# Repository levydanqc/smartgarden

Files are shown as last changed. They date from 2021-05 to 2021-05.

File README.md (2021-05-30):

Quick links:

- [Latest release](https://github.com/levydanqc/smartgarden/releases/latest)
- [GitHub](https://github.com/levydanqc/smartgarden)
- [Arduino Projet](https://arduino-esp8266.readthedocs.io/en/latest/)
- [TODO](TODO.md)

===========================================

# SmartGardener

Smart garden monitoring system for growing vegetables and fruits with an NodeMcu and Blynk platform.

## My Story

At some points in life, we all tried to do some sort of gardening. Whether it is to embellish our house, to tried to grow some food or to prove to ourselves that we're able to take care of something else and not let it die, the process of planting some seeds in the ground isn't easy.
The problem is that humankind isn't the most reliable. How many of us forgot to take the cake out of the oven, to put the lid back on the peanut butter jar or even to water the plants and thought "Man ! Not again.". What if I told you there is an other way ? Today's technology let us automate virtually anything, from turning on and off the lights, brewing coffee each morning or cooking delicious meal.
Combining automation, micro-controllers and plants isn't new, there's plenty of projects on the internet about people trying to create their own garden monitoring system. Mine isn't that much different than theirs except that for one, almost everything is combined together. I've searched for a project where there would be soil moisture sensors, lights sensors, solenoid water valve, etc. as well as being able to control everything remotely before deciding to build my own.
It does work like I wanted, but there is so much more sensors and logic that I could and would like to add to this project, like TDS sensor (for water quality), controlling multiples valve for multiples garden, but one thing at a time.

## Connections

Because there's actually a lot of sensors (and I'm not that good with layout..), below is all the connections for the project.
_In the Schemas folder, there is a schema for the connections of each sensors._

| Board | Vin | Gnd | A0 | D0 | D1 | D2 | D5 | D6 | D7 |
| --- | :-: | :-: | :---: | :---: | :---: | :---: | :----: | :----: | :----: |
| NodeMcu | 12V | Gnd | MUX:COM(Z) | Flow:Data | DHT11:Data | Mosfet:Gate | MUX:S0 | MUX:S1 | MUX:S2 |

| Components  | Vcc | Gnd | COM (Z) | S0  | S1  | S2  | CH0 | CH1 | CH2  | CH3  |
| --- | :-: | :-: | :-----: | :-: | :-: | :-: | :-: | :-: | :--: | :--: |
| Multiplexer | 12V | Gnd | A0 | D5  | D6  | D7  | SM1 | SM2 | LDR1 | LDR2 |

| Components | Gate | Source |  Drain |
| --- | :---: | :----: | :---: |
| Mosfet | D2 (PU-10) |  Gnd | Valve[-] |

| Components | Positive | Negative | Data | Infos |
| --- | :---: | :---: | :--: | :---: |
| Power supply | Vin | Gnd | | |
| |  Valve | Gnd | | |
| | SD:In[+] | Gnd | | |
| Valve | 12V | Gnd | | |
| Diode | Valve[+] | Valve[-] | | |
| DHT11 | 3V | Gnd |  D1  | PU-10 |
| Soil Moisture 1 | 3V | Gnd | CH0  | |
| Soil Moisture 2 | 3V | Gnd | CH1  | |
| Photocell 1 | 3V | Gnd | CH2  | PD-1  |
| Photocell 2 | 3V | Gnd | CH3  | PD-1  |
| Flow Sensor | 3V | Gnd |  D0  | |

<dl>
  <dt>SM</dt>
  <dd>Soil Moisture Sensor.</dd>
  <dt>LDR</dt>
  <dd>Light Dependant Resistor (Photocell).</dd>
  <dt>MUX</dt>
  <dd>Multiplexer.</dd>
  <dt>SD</dt>
  <dd>Step-Down Converter.</dd>
  <dt>PU-Value</dt>
  <dd>Pull-Up Resistors of _Value_ kΩ.</dd>
  <dt>PD-Value</dt>
  <dd>Pull-Down Resistors of _Value_ kΩ.</dd>
</dl>

_12V refers to the power supply._ | _3V to the output of the NodeMcu._
_Ground connections are not important as long as they are wired together._ <br>
**Please make sure to double check your wiring before connecting the power supply as a wrong connection could fry your components. Also make sure to check all pull-down or pull-up resistors on the schema.**

## Configuration

To configure the project, all you need to do is enter your own informations from line 17 to 20. You will need the name and password of your WIFI and a hostname for the board as well as a password that you can create (It is optional, but for security purposes we were more comfortable using one).
The hostname will appear in the PORT setting of the Arduino IDE when you want to upload code and the password will be asked after compiling, just before uploading.

## Over-the-Air (OTA) Upload

The NodeMcu will be placed inside a waterproof and weather-resistant box near the plants and a power outlet so it won't be
easily accessible. A library called ArduinoOTA (Over-the-Air) let us upload new code to the board without being physically
connected to it, we only need to be in the same network for that to work.
The first upload need, obviously, to be wired to the board, but after that we can select the NodeMcu in the PORT configuration of the Arduino IDE to be connected to it.

**It is important to upload the OTA code and librairies each time to be sure it will still be accessible.**

## Flow Sensor

The flow sensor is being used primarily for testing the opening command of the valve.
It precision or accuracy isn't really what matters most as any value means the valve was opened and the system is working well.
His working principle is based on the Hall Effect: there is a rotor inside that makes loop when water goes though it with a magnet on one of the propeller and it outputs a signal each time the magnet complete one loop.

In the datasheet of the sensor there is coefficient often written like: `F = 7.5Q`. This number represents the quantity of water that has passed for each loop and is used to calculate the flow rate.

The formula is quite simple:

```
Flow rate (L/min) = Nb of loop for 1 sec / flow coefficient.
```

In this program, we used `attachInterrupt()` function from the arduino library that can asynchronously do a task when a physical pin receive a signal. Because of the way Blynk works we cannot use the `delay()` function to wait 1 second so instead, we began the interrupts (so that it increment a variable each time the signal is received) and at the next iteration we stop the interrupts and start calculate the flow rate using the actual time passed from the moment started it.

The adapted formula is then:

```
Flow rate (L/min) = ((1000.0 / (now() - start)) * count) / flowQ.
```

_We need to convert the number of loop from the nuber of seconds it was measure to 1 second._
_Where now() is the current time in unix (since epoch), start is the time we start counting signals (also in unix), count is the number of loop the magnet did and flowQ is the flow sensor coefficient._

## Soil Moisture Sensor

To calibrate the soil moisture sensor:

1. Put sensor in the air, retrieve value and set it to MOISTURE_AIR
2. Put sensor in water, retrieve value and set it to MOISTURE_WATER

## Solenoide Water Valve

The water valve need a 12V power supply and about 600 mA, but each items is different
so check your datasheet to be sure. Also, there is no polarity so you can connect either pin
to ground and positive.

## Mosfet IRF540N

A simple NPN transistor cannot take the power the solenoid valve needs, that is why a mosfet transistor is used. We control the solenoid valve with the Gate pin of the mosfet that, when HIGH, let current flow between Source and Drain.

## Multiplexer CD74HC4051

The NodeMcu only has one analog input, but there's 5 analog sensors to connect. That's when the multiplexer enter!
A multiplexer gives the possibility to connect multiples analog input to only one output. It does so by controlling which
sensor is poweredm (one at a time), reading its value and sending it before continuing to the next one.
This one has 8 channel, this means we can connect up to 8 analog inputs through the 8 pins _Y_ or _CH_ and output the value
through the _COM_ or _Z_ pin. We can tell it what channel to read from by controlling the state of the 3 _S_ pins, by pulling them
up in a specific way, it powered the matching channel.
Below is a table for each combination (it is basically a binary table with 3 bits):

| S0  | S1  | S2  | Channel |
| --- | :-: | :-: | :-----: |
| 0 |  0  |  0  | 0 |
| 1 |  0  |  0  | 1 |
| 0 |  1  |  0  | 2 |
| 1 |  1  |  0  | 3 |
| 0 |  0  |  1  | 4 |
| 1 |  0  |  1  | 5 |
| 0 |  1  |  1  | 6 |
| 1 |  1  |  1  | 7 |

## [Installation of Blynk Local Server](https://github.com/blynkkk/blynk-server)

For my project we used the Blynk Local Server. The installation can be found [on their GitHub](https://github.com/blynkkk/blynk-server) and it is pretty straight-forward.
The advantages of using your own local server is that you have a full control on what's happening, on the data that is being retrieved (could be
useful if like GPS was enabled on the app) so that your data isn't stored inside blynk server. Also, it is actually faster to use a local server
because of the distance the signal has to travel and more importantly, you can have as much Blynk Energy you want (so that you can customize your app by
adding an infinite number of widgets).

---

## © Copyright

<dl>
  <dt>Adidax: DHT11 Library</dt>
  <dd><a href="https://github.com/adidax/dht11">Github</a></dd>
  <dt>Blynkkk: Blynk-library</dt>
  <dd><a href="https://github.com/blynkkk/blynk-library">Github</a></dd>
  <dt>How2Electronics: TDS Meter</dt>
  <dd><a href="https://how2electronics.com/iot-based-tds-meter-using-esp8266-for-water-quality-monitoring/">Github</a></dd>
  <dt>The HookUp: GPIO_Limitations_ESP8266_NodeMCU.jpg</dt>
  <dd><a href="https://github.com/thehookup/Wireless_MQTT_Doorbell/blob/master/GPIO_Limitations_ESP8266_NodeMCU.jpg">Github</a></dd>
</dl>

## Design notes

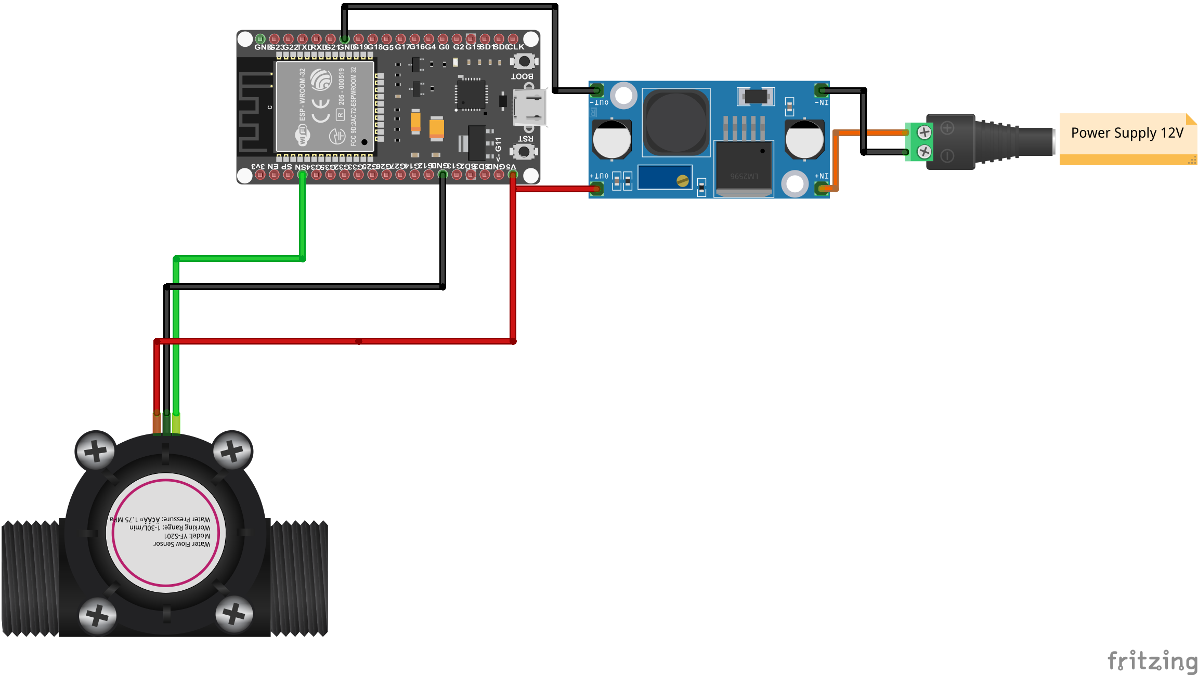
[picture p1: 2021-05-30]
Schematics/flow_sensor.png

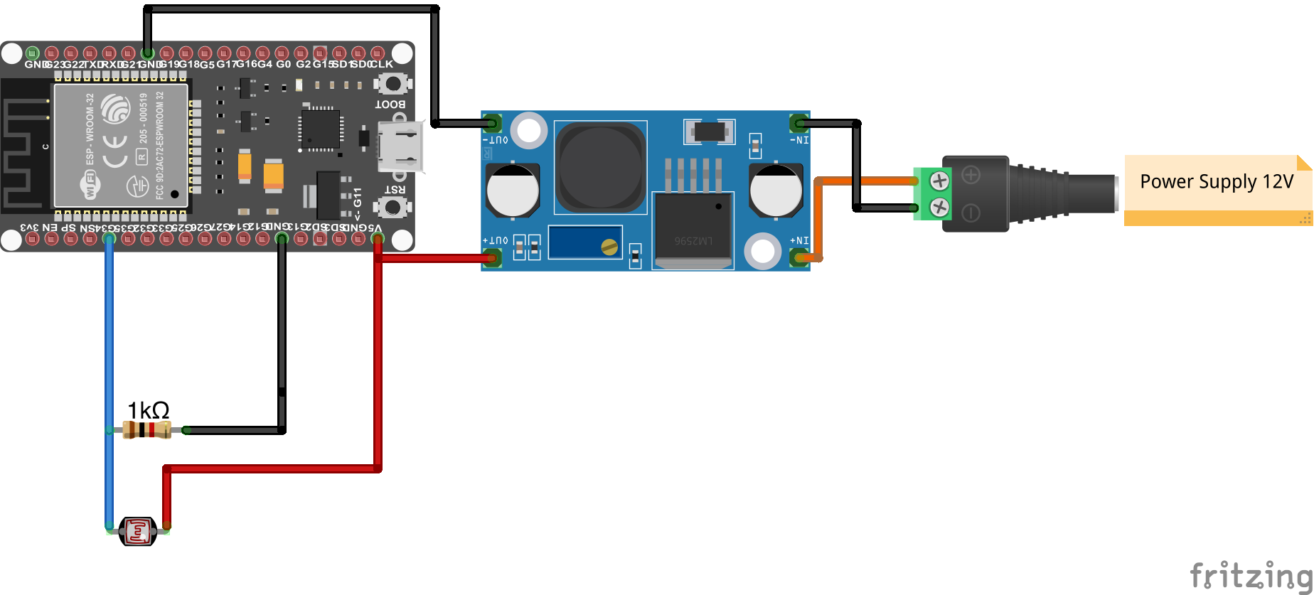
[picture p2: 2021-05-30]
Schematics/photocell.png

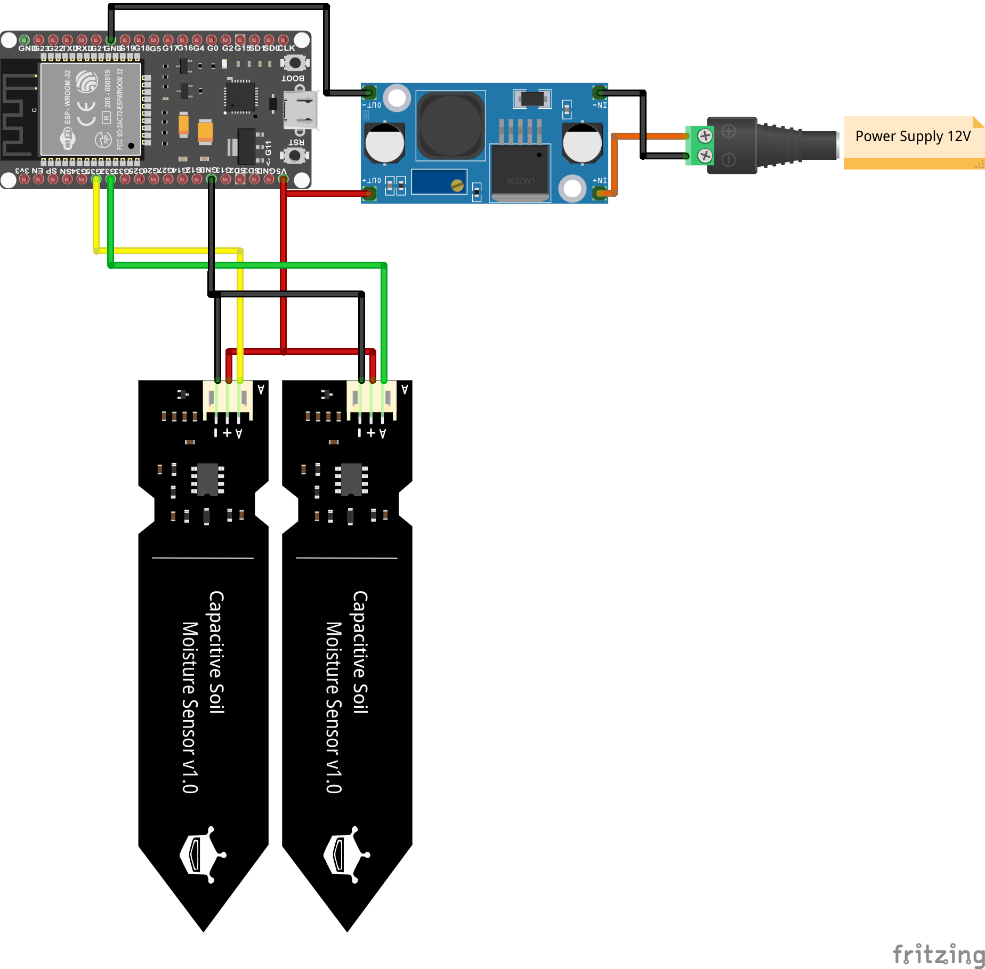
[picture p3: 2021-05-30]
Schematics/moisture_sensors.png

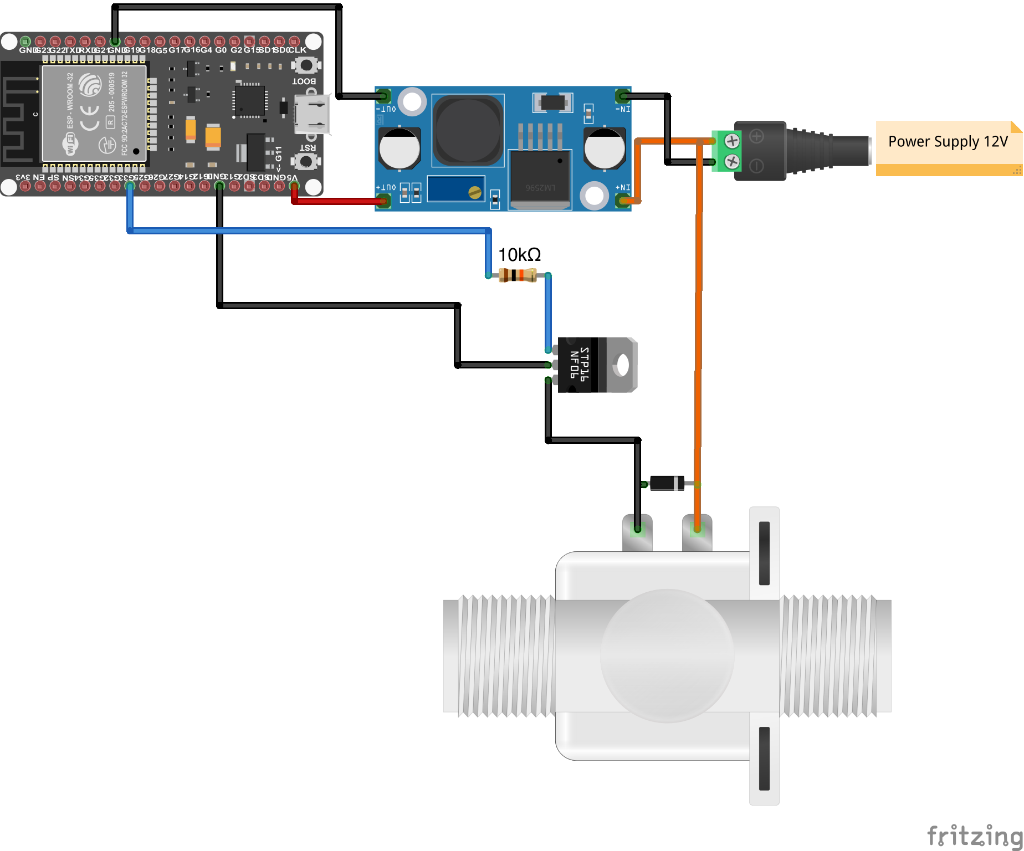
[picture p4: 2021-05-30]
Schematics/solenoid_valve.png

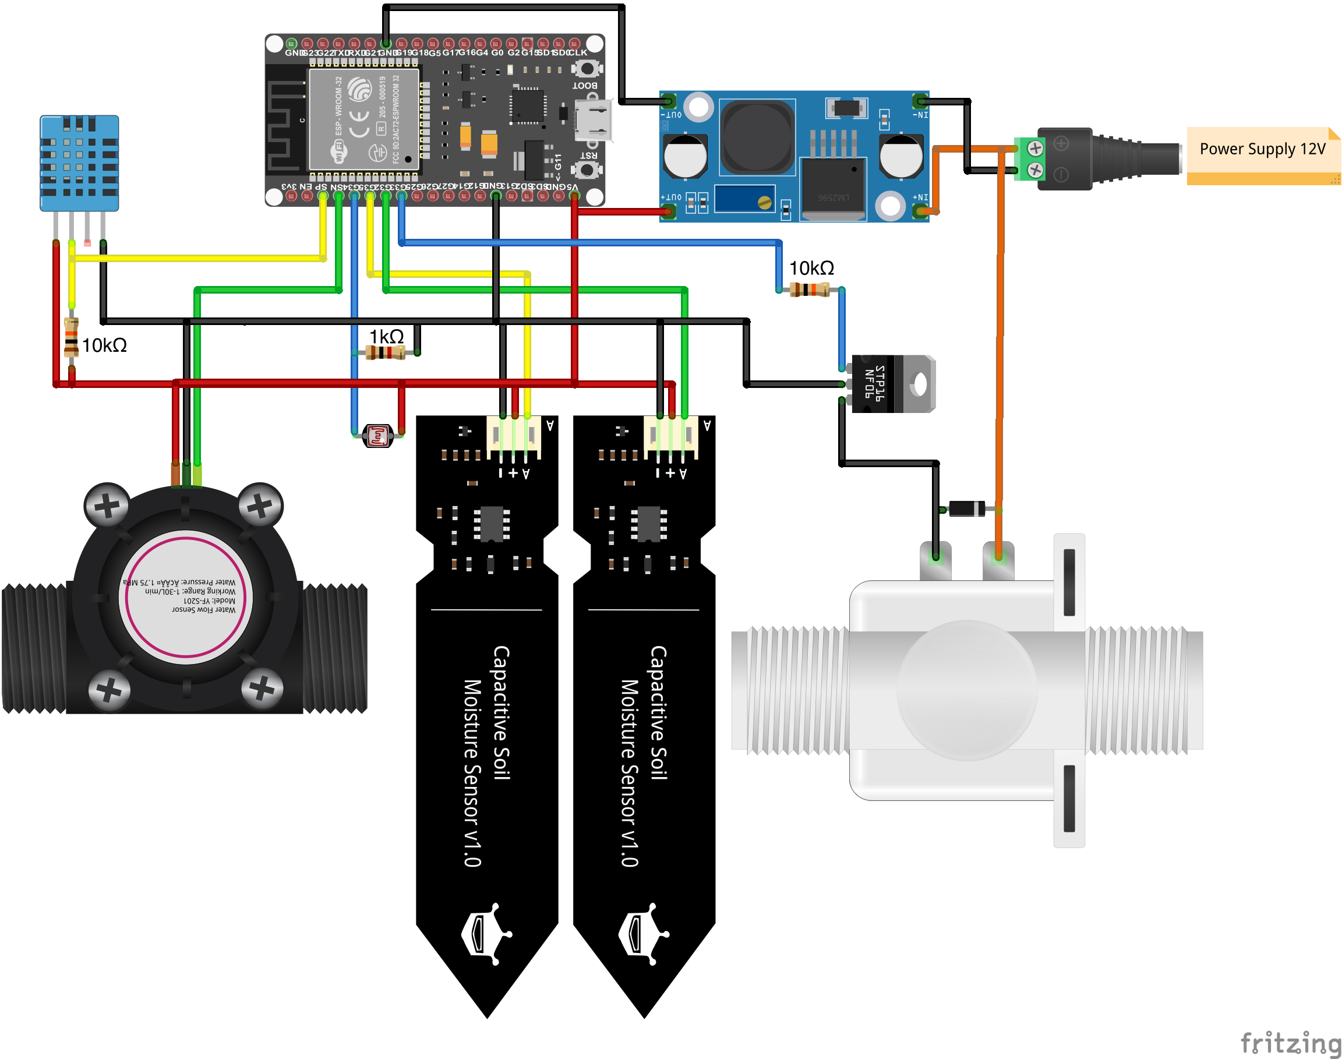
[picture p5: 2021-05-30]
Schematics/SmartGardener.png

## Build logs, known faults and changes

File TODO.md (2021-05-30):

# TODO list

Ideas of what to add for the future.

### In Progress

- [ ] Create file for soil moisture calibration

### For the future

- [ ] Get forecast weather
- [ ] Optimize variable size

### Done ✓

- [x] Switch valve with duration
- [x] Add a notification when online

### Personal Notes

Send notification with Blynk: Blynk.notify(message)
Send email with Blynk: Blynk.email("to@example.com", "Subject", "Your message goes here");

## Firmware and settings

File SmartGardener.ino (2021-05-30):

/***************************************************

 * Smart Garden Monitoring


 ** https://gitlab.com/levydanqc/smartgarden 

 ****************** Configuration ******************
Line 25:    SSID "PASSWORD_FOR_THE_ARDUINO"             -->     Name of your network
Line 26:    PASSW "YOUR_WIFI_PASSWORD":                 -->     Password of your network
Line 27:    ArduinoOTAHostname "NAME_FOR_THE_ARDUINO":  -->     Hostname for the OTA PORT setting
Line 28:    ArduinoOTAPASSW "PASSWORD_FOR_THE_ARDUINO": -->     Password for the OTA upload
Line 35:    char auth[] = "YOUR_BLYNK_TOKEN":           -->     Authentication token of the Blynk project

 ****************************************************
  © Copyright : see README.md
****************************************************/
/* 
 * Uncomment next line for debugging connection issues.
 * It will print to serial information about WIFI connection
 * and local server. 
*/
#define BLYNK_PRINT Serial

// ESP32
#include <WiFi.h>
#include <WiFiClient.h>
#include <BlynkSimpleEsp32.h>
#include <TimeLib.h>
#include <WidgetRTC.h>

// For OTA upload
#include <ESPmDNS.h>
#include <WiFiUdp.h>
#include <ArduinoOTA.h>

#include "dht11.h"

/* OTA Setup */
#ifndef SSID
#define SSID "YOUR_WIFI_SSID"                      // Enter the name of your network as it is in you WIFI settings
#define PASSW "YOUR_WIFI_PASSWORD"                 // Enter the password of your network
#define ArduinoOTAHostname "NAME_FOR_THE_ARDUINO"  // Enter the hostname for the board (Optional)
#define ArduinoOTAPASSW "PASSWORD_FOR_THE_ARDUINO" // Enter the password for the board (Optional)
#endif
const char *OtaSSID = SSID;
const char *OtaPassw = PASSW;
/* END OTA */

/* Blynk Setup*/
char auth[] = "YOUR_BLYNK_TOKEN";
char ssid[] = SSID;
char pass[] = PASSW;
BlynkTimer timer;
WidgetTerminal terminal(V13);
WidgetRTC rtc;
byte sliderValue;
float inputValue;
/* END Blynk */

/* Pinout */
#define valvePin 33
#define moisturePin1 32
#define moisturePin2 34
#define ldrPin 35
#define flowPin 39
#define dhtPin 36
/* END Pinout */

/* Function */
const byte inputs = 5;
float (*func[])(){
    getMoisture1,
    getMoisture2,
    getLDR,
    getFlow,
    getTemp,
    getHum};
/* END Function */

/* Valve */
unsigned long startValve;
int duration;
int valveIsActivated;
/* END Valve */

/* Flow Sensor */
volatile byte flowCounter;
float flowQ = 7.5;
float startFlow;
float flowRate;
/* END Flow */

/* DHT11 Sensor */
dht11 Dht;
float humidity;
float temperature;
/* END DHT11 */

/* Moisture Sensor */
#define MOISTURE_WATER 300
#define MOISTURE_AIR 670
float moisture1;
float moisture2;
/* END Moisture */

/* LDR */
#define LDR_MIN 0
#define LDR_MAX 1000
float ldr1;
/* END LDR */

void setup()
{
    Serial.begin(9600);

    /* OTA Setup */
    WiFi.mode(WIFI_STA);
    WiFi.begin(OtaSSID, OtaPassw);
    while (WiFi.waitForConnectResult() != WL_CONNECTED)
    {
        Serial.println("Connection Failed! Rebooting...");
        delay(5000);
        ESP.restart();
    }
    ArduinoOTA.setHostname(ArduinoOTAHostname);
    ArduinoOTA.setPassword(ArduinoOTAPASSW);
    /* END OTA */

    /* Blynk Setup */
    Blynk.begin(auth, ssid, pass, "192.168.1.100", 8080);
    timer.setInterval(1000L, sendData);
    terminal.println("Connecté!");
    /* END Blynk */

    /* OTA Setup */
    ArduinoOTA.onStart([]() {
        String type;
        if (ArduinoOTA.getCommand() == U_FLASH)
        {
            type = "sketch";
        }
        else
        { // U_FS
            type = "filesystem";
        }

        // NOTE: if updating FS this would be the place to unmount FS using FS.end()
        Serial.println("Start updating " + type);
    });
    ArduinoOTA.onEnd([]() {
        Serial.println("\nEnd");
    });
    ArduinoOTA.onProgress([](unsigned int progress, unsigned int total) {
        Serial.printf("Progress: %u%%\r", (progress / (total / 100)));
    });
    ArduinoOTA.onError([](ota_error_t error) {
        Serial.printf("Error[%u]: ", error);
        if (error == OTA_AUTH_ERROR)
        {
            Serial.println("Auth Failed");
        }
        else if (error == OTA_BEGIN_ERROR)
        {
            Serial.println("Begin Failed");
        }
        else if (error == OTA_CONNECT_ERROR)
        {
            Serial.println("Connect Failed");
        }
        else if (error == OTA_RECEIVE_ERROR)
        {
            Serial.println("Receive Failed");
        }
        else if (error == OTA_END_ERROR)
        {
            Serial.println("End Failed");
        }
    });
    ArduinoOTA.begin();
    terminal.print("IP address: ");
    terminal.println(WiFi.localIP());
    /* END OTA */

    /* Flow Sensor Setup */
    attachInterrupt(digitalPinToInterrupt(flowPin), FlowIncrement, RISING); // Create interrupts
    noInterrupts();                                                         // Disable interrupts at beginning
    /* END Flow */

    terminal.flush();
}

void loop()
{
    ArduinoOTA.handle();
    Blynk.run();
    timer.run();
}

/**
    Point d'entrée de Blynk.

    Écrit chaque donnée sur les pins virtuelles
    de blynk.
*/
void sendData()
{
    // Get data from sensors
    for (int i = 0; i <= inputs; i++)
    {
        Blynk.virtualWrite(i, (func[i])());
    }

    // Check valve opening duration
    if (valveIsActivated && duration != -1 && now() >= (startValve + duration))
    {
        valveIsActivated = false;
        terminal.println("Closed valve after duration.");
        terminal.flush();
        toggleValve();
    }
    // Check flow rate to verify that the valve was opened
    if (valveIsActivated && flowRate < 5)
    {
        //Blynk.notify("Erreur d'ouverture de la valve. Débit trop faible.");
    }

    // Notify if valve opened for a certain time (like if user inputs is too big)
    int openedDuration = now() - startValve;
    if (valveIsActivated && openedDuration > 0 && (openedDuration % (60 * 60) == 0)) // Every hour
    {
        //Blynk.notify("La valve est ouverte depuis " + String(openedDuration / 60) + " minutes.");
    }
}

/**
    Get soil moisture from sensor 1 in percent.

    @return Soil moisture from sensor 1 in %.
*/
float getMoisture1()
{
    for (int i = 0; i < 100; i++) // Retrieving a hundred value for accuracy
    {
        moisture1 += analogRead(moisturePin1);
        delay(1);
    }
    moisture1 = moisture1 / 100.0; // Get average value
    // Map value between 0 and 100 to get a percentage
    moisture1 = map(moisture1, MOISTURE_AIR, MOISTURE_WATER, 0, 100);
    return constrain(moisture1, 0, 100); // Constrain value inside [0, 100]
}

/**
    Get soil moisture from sensor 2 in percent.

    @return Soil moisture from sensor 2 in %.
*/
float getMoisture2()
{
    for (int i = 0; i < 100; i++) // Retrieving a hundred value for accuracy
    {
        moisture2 += analogRead(moisturePin2);
        delay(1);
    }
    moisture2 = moisture2 / 100.0; // Get average value
    // Map value between 0 and 100 to get a percentage
    moisture2 = map(moisture2, MOISTURE_AIR, MOISTURE_WATER, 0, 100);
    return constrain(moisture2, 0, 100); // Constrain value inside [0, 100]
}

/**
    Get light intensity from sensor 1 in percent.

    @return Light intensity from sensor 1 in %.
*/
float getLDR()
{
    for (int i = 0; i < 100; i++)
    {
        ldr1 += analogRead(ldrPin);
        delay(1);
    }
    ldr1 = ldr1 / 100.0;
    ldr1 = map(ldr1, LDR_MIN, LDR_MAX, 0, 100);
    return constrain(ldr1, 0, 100);
}

/**
   Increment the number of loop of the magnet by one.
*/
ICACHE_RAM_ATTR void FlowIncrement()
{
    flowCounter++;
}

/**
   Get flow rate from sensor in L/min.

    @return Flow rate in L/min or 0 if valve isn't opened yet.
*/
float getFlow()
{
    if (valveIsActivated)
    {
        if (startFlow == 0)
        {
            startFlow = now();
            interrupts();
            return flowRate * valveIsActivated; // Return 0 if valve is closed, flow rate otherwise
        }
        else
        {
            noInterrupts();
            flowRate = ((1000.0 / (now() - startFlow)) * flowCounter) / flowQ; // Flow rate in L/min
            startFlow = 0;
            return flowRate * valveIsActivated; // Return 0 if valve is closed, flow rate otherwise
        }
    }
    return 0;
}

/**
    Get humidity from DHT11 sensor.

    @return Humidity from DHT11 in %.
*/
float getTemp()
{
    Dht.read(dhtPin);              // Retreive value
    return (float)Dht.temperature; // Return humidity
}

/**
    Get temperature from DHT11 sensor.

    @return Temperature from DHT11 in °C.
*/
float getHum()
{
    Dht.read(dhtPin);           // Retreive value
    return (float)Dht.humidity; // Return humidity
}

/**
    Togge between state (open/close) of valve and print it to terminal.
*/
void toggleValve()
{
    String state;
    switch (valveIsActivated)
    {
    case 0:
        state = "closed";
        break;
    case 1:
        state = "opened";
        break;
    }

    terminal.println("Valve " + state + " @ " + getTime());
    terminal.flush();

    digitalWrite(valvePin, valveIsActivated);  // Open/Close valve
    Blynk.virtualWrite(V14, valveIsActivated); // Blynk chart of valve state
    if (duration != -1)
    {
        Blynk.virtualWrite(V10, valveIsActivated);
    }
    else
    {
        Blynk.virtualWrite(V10, 0);
    }
}

/**
   Return current date and time inside a string.
*/
String getTime()
{
    String date = String(day()) + "/" + month() + "/" + year();
    String time = String(hour()) + ":" + minute() + ":" + second();
    return date + ' ' + time;
}

/* Blynk functions  */
/**
    Run when connected to Blynk.
    Synchronize clock.
*/
BLYNK_CONNECTED()
{
    rtc.begin();
    for (byte i = 0; i < 13; i++)
    {
        Blynk.virtualWrite(i, 0);
    }
}

/**
    Run when changes on numeric input.
    Store input value for duration in hours.
*/
BLYNK_WRITE(V7) // Numeric Input
{
    inputValue = param.asFloat();
    int totalMinutes = (sliderValue % 60) + (inputValue - (int)inputValue) * 60;
    Blynk.virtualWrite(V11, ((int)inputValue + (sliderValue / 60) + (totalMinutes / 60)));
    Blynk.virtualWrite(V12, (totalMinutes % 60));
}

/**
    Run when changes on slider.
    Store slider value for duration in minutes.
*/
BLYNK_WRITE(V8) // Slider
{
    sliderValue = param.asInt();
    int totalMinutes = (sliderValue % 60) + (inputValue - (int)inputValue) * 60;
    Blynk.virtualWrite(V11, ((int)inputValue + (sliderValue / 60) + (totalMinutes / 60)));
    Blynk.virtualWrite(V12, (totalMinutes % 60));
}

/**
    Run when activation button is pressed.
    Activate/Deactivate valve.
*/
BLYNK_WRITE(V10) // Input Activation button
{
    if (duration != -1) // Timer not running
    {
        valveIsActivated = param.asInt();
        if (valveIsActivated) // Start valve
        {

            duration = (sliderValue + (int)(inputValue * 60)) * 60; // Total duration in seconds
            startValve = now();                                     // Get unix time (in seconds)
            terminal.println("Manually opened valve.");
            terminal.flush();
            toggleValve();
        }
        else
        {
            duration = 0;
            startValve = 0;
            terminal.println("Manually closed valve.");
            terminal.flush();
            toggleValve();
        }
    }
    else
    {
        Blynk.notify("Timer currently running.");
    }
}

/**
   Run when timer is activated.
   Adapt duration for timer and open/close valve.
*/
BLYNK_WRITE(V9) // Timer button
{
    if (startValve == 0) // Activation button not running
    {
        valveIsActivated = param.asInt();

        duration = 0 - valveIsActivated; // duration = -1 when running, 0 otherwise
        terminal.println("Timer toggled valve.");
        terminal.flush();
        toggleValve();
    }
    else
    {
        Blynk.notify("Manual button currently running.");
    }
}

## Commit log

2021-04-14 Ajout des fichiers initiaux.
    [SmartGarden.fzz]
2021-04-17 Added TDS sensor.
2021-04-17 Added DHT11 sensor.
2021-04-17 Added Soil Moisture sensor.
2021-04-17 Added LDR sensor.
2021-04-17 Added multiplexer and fixing blynk.
    [SmartGarden.fzz]
2021-04-17 Updated README.md.
    [SmartGarden.fzz]
2021-04-18 Removing TDS library.
    [SmartGarden.fzz]
2021-04-22 Added valve activation/deactivation.
    [SmartGarden.fzz]
2021-04-25 Replacing TDS Sensor for Flow Sensor.
    [SmartGarden.fzz]
2021-04-25 Added Individual Schematics.
    [dht11.fzz, flow_sensor.fzz, moisture_sensors.fzz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]
2021-04-28 Replacing Transistor with Mosfet.
    [SmartGarden.fzz]
2021-05-07 Fixing valve duration.
2021-05-08 Modified README.md.
    [SmartGardener.fzz]
2021-05-08 Adding Schematics Images.
    [SmartGardener.fzz, dht11.fzz, flow_sensor.fzz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]
2021-05-30 Replacing ESP8266 for ESP32.
    [SmartGardener.fzz, dht11.fzz, flow_sensor.fzz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]
